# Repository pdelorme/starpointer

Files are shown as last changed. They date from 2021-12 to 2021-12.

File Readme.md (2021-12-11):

StarPointer
===========

StarPointer is a small 3D printed autonomous device that allows one to point and track sky objects (planets, shiny Messier objects, ISS) with a laser.

it's properies are :
- fully 3D printed.
- controlled by ESP8266 or ESP32
- motorized with 2 Stepper 28byj-48
- WIFI Access Point or Client
- Responsive Web interface.
- ISS tracking data auto-update.
- Dynamic tracking of objects.
- Persitence of configuration in EEPROM
- Low power (simple 5V powerpack)

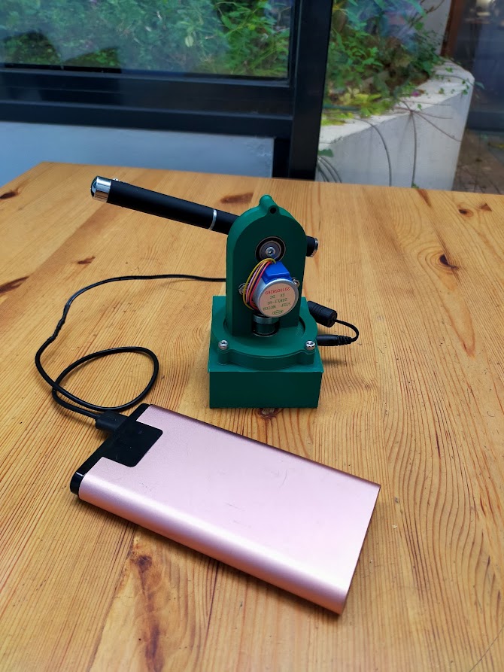
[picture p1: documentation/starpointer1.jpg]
Star pointer


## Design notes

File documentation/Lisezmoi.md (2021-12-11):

Documentation
===

StarPointer est concu pour etre calibré manuellement quelque soit son orientation.
Le seul prérequis est d'avoir l'etoile polaire en visuel.

Connexion
---
Lors de sa premiere mise sous tension le startPointer creera un Acces Point WIFI
- SSID : STAR_POINTER
- MdP  : 1234567890
- IP   : 192.168.4.1

Connectez vous-y avec votre navigateur PC ou mobile : http://192.168.4.1/

Configuration
---
StarTracker à besoin de connaitre votre position géographique et l'heure pour tous ses calculs astronomiques.

Dés votre connexion, le StarPointer recuperera l'heure de votre PC ou mobile pour se configurer.
Vous pouvez constater l'heure prise en compte sur l'interface.

Vous devrez configurer votre position géographique manuellement avec le dropdown de positions connues.

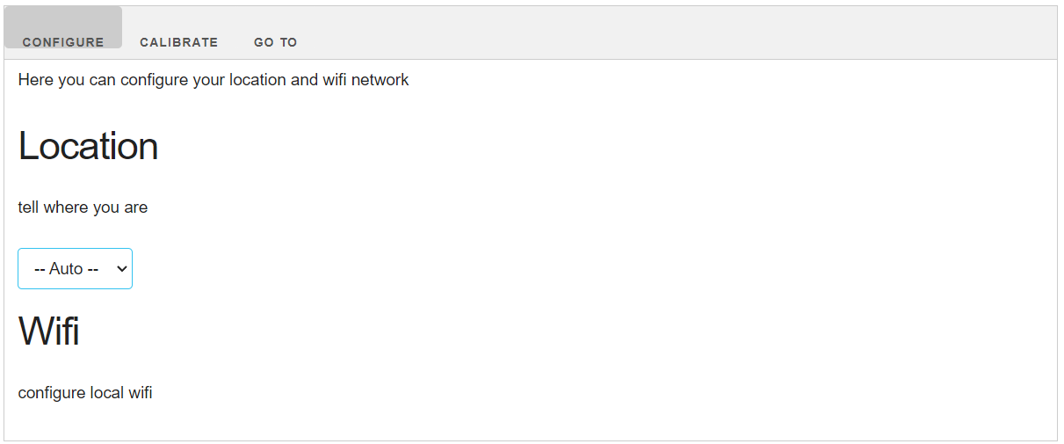
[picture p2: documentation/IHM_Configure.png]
Configure


Calibration
---
Une fois l'apareil configuré, vous devez le calibrer pour qu'il sache ou est le nord celeste.

Sur l'onglet calibration
  1. appuyez sur "Goto Polaris". Le startracker se déplacera vers ce qui est polaris pour lui. initialement cette position est aléatoire.
  2. orientez le startracker pour que le pointeur laser pointe aproximativement dans la direction du nord.
  3. à l'aide des touches UP, DOWN, LEFT, RIGH, déplacez le pointeur pour qu'il pointe le plus pécisément possible sur l'étoile polaire.
  4. une fois l'alignement satisfaisant, appuyez sur "set polaris position"
Le startracker est maintenant calibré.

Vous pouvez vérifier son bon fonctionnement grace aux boutons North, south, east, west, horizon et azimuth qui déplacerons le laser vers la dircetion choisie.

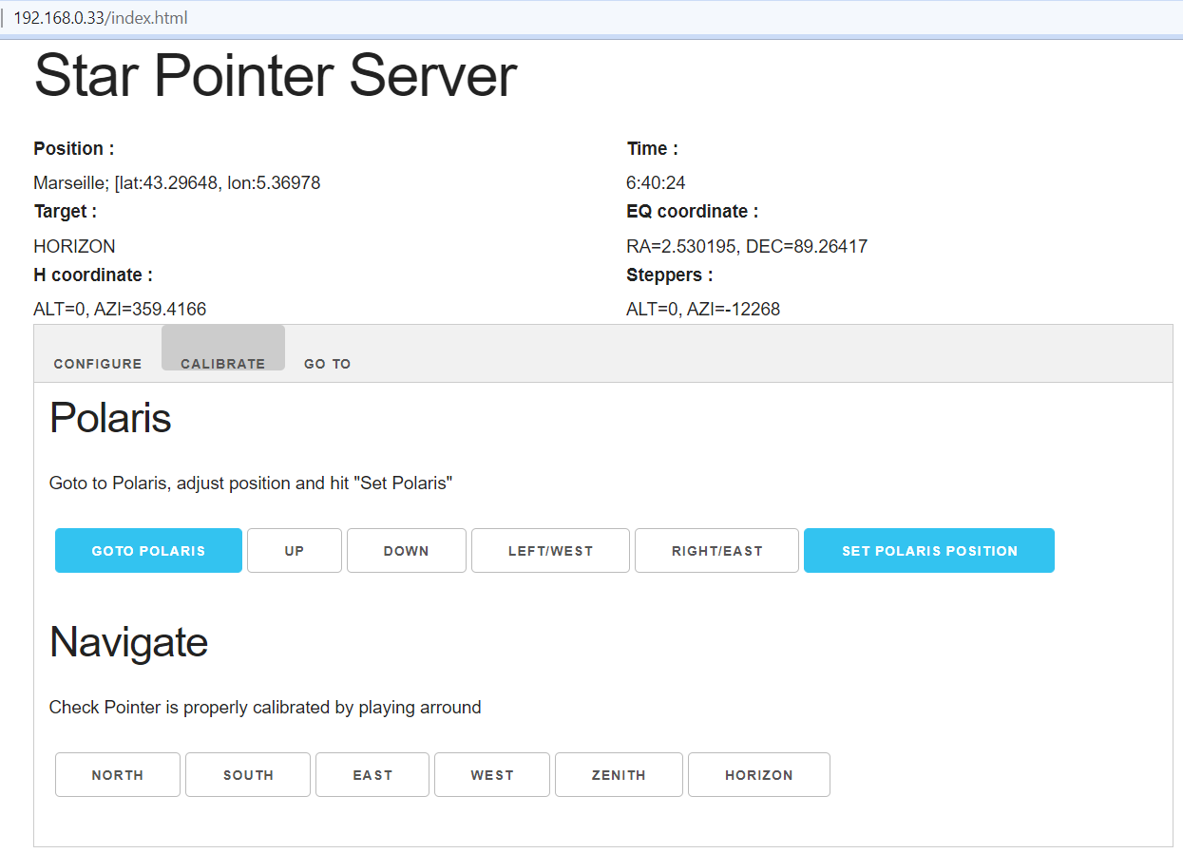
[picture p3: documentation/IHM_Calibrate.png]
Calibrate


Tracking
---
L'onglet goto sert à controler le startPointer une fois bien configuré.

Choisisez une target et laissez le starPointer aller à la cible puis la suivre.

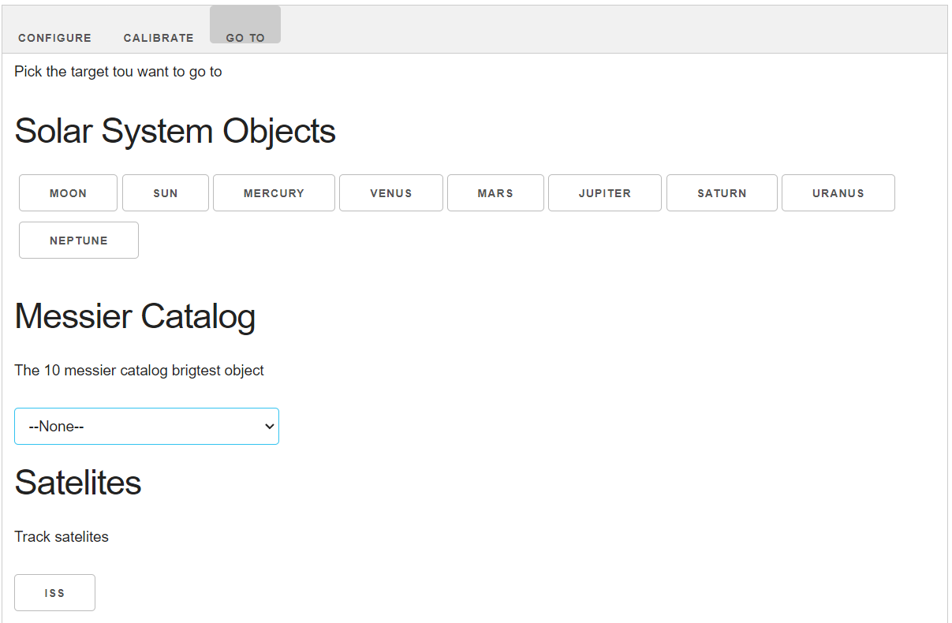
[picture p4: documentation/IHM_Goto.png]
Go To


Note
---
- Starpointer est contraint au dessus de l'horizon (une fois calibré). si votre cible est en dessous de l'horizon. il la suivra mais sans aller en dessous de l'horizon.

- Le calcul de la trajectoire de l'ISS dépend de données online qui doivent etre rafraichie régulierement pour etre valide. Pour se faire vous devrez connecter votre starpointer à internet avant une session d'observation.

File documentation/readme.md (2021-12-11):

Documentation
===

Starpointer is designed to be calibrated manually whatever his position and location is.
The only requierment is to be able to see polaris from the device.

Connexion
---
StarPointer will create the flowing WIFI access point at first boot or when the local AP cannot be fount.
- SSID : STAR_POINTER
- MdP  : 1234567890
- IP   : 192.168.4.1

Connect to StarPointer by going to http://192.168.4.1/ with your favorite browser on PC or mobile.

Configuration
---
StarPonter need to know where and when it is in order to do its astonomic calculations.

On connection, StarTracker will get time and location from your browser.
You can check that time is correct in the interface.
If geo-coordinate is not found, you can set it manually from the location drowpdown or by inputing your coordinates.

Configure

Calibration
---
Once configured, you must caibrate your device so it knows where celestial north is.

1. Go to "Calibration"
2. push "Goto Polaris". StarPointer will move to where it thinks polaris is (which is random at first)
3. move the device to point more or less north.
4. using the UP, DOWN, LEFT, RIGH buttons, move the poiter so it aligns perfectly with polaris.
5. push "set polaris position" when you are done.

StarPointer is now calibrated. 

You can use the North, south, east, west, horizon and azimuth buttons to check the StarPointer is behaving as exppected.

Calibrate

Tracking
---
This tab is for pointing the device at some space objects.

Pick the object you want to point to and StarPointer will move to it.
Once aligned with the target StarPointer will stay in synch and will update it pointing every seconds.

Go To

Note
---
- Starpointer is constrained above horizon (once calibrated). If your target is below the horizon, it will track it while staying stuck at the horizon level.
- ISS trajectory needs some fresh online update to be accurate. Therefore StarPointer has to be connected to local Wifi network in order to refresh its reference data. It'll try to do so each time you connect to a local network.

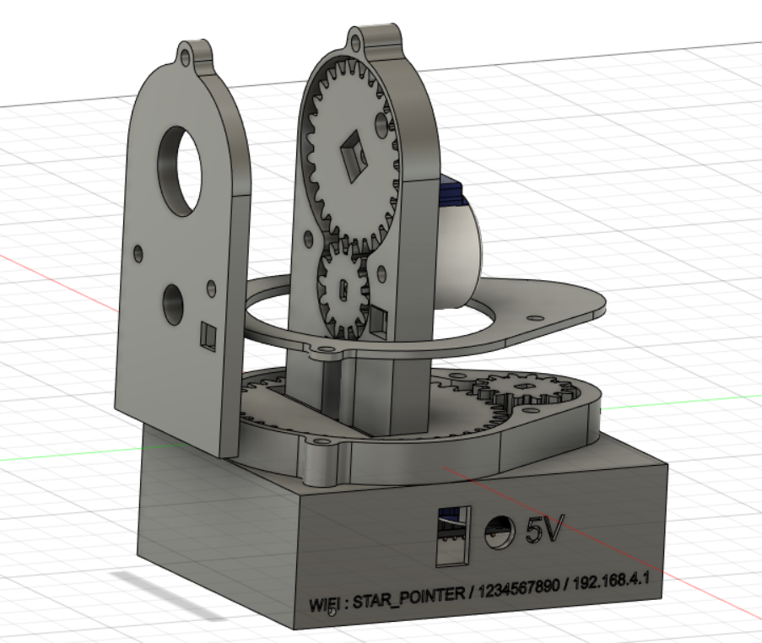
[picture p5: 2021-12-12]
3d/3DModel.png

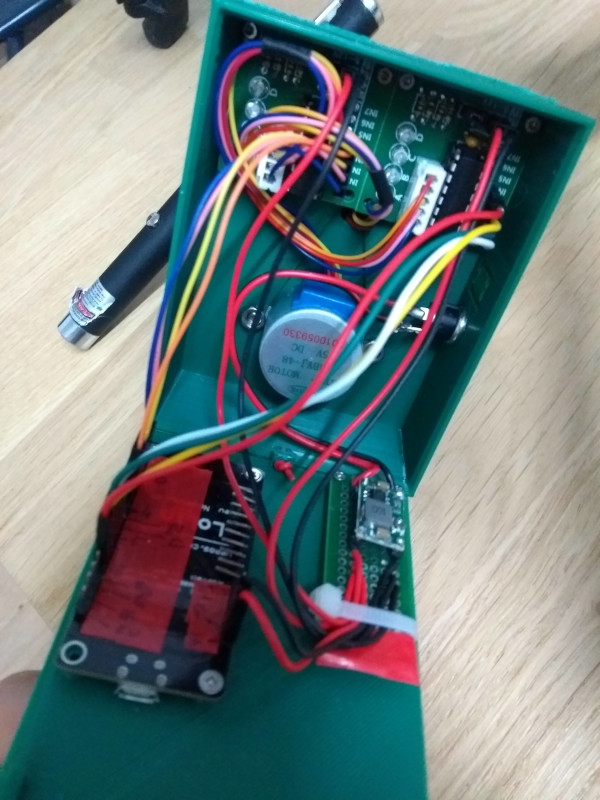
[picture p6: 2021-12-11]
fritzing/Photo inside.jpg

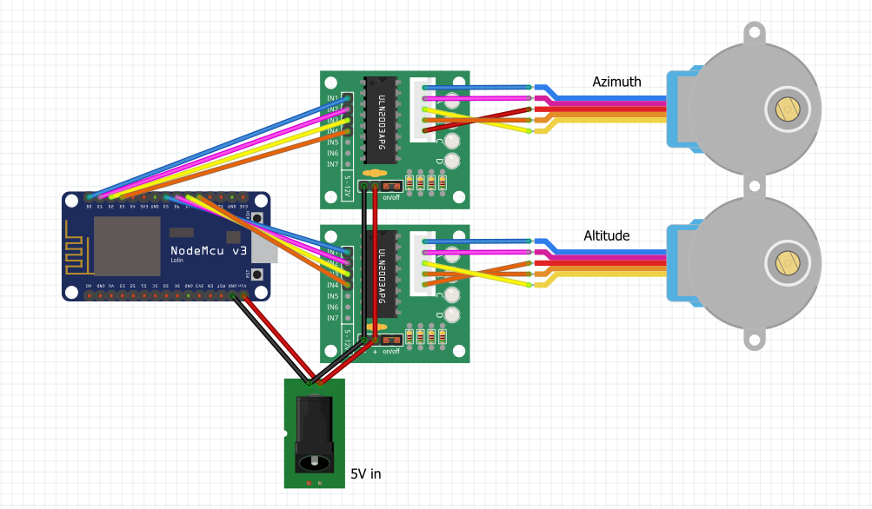
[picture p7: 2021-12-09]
documentation/Schema v1.png

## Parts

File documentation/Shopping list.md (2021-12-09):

Shopping list
===

Stylo Laser Vert de Haute Puissance de 5MW et 650 nm
https://fr.aliexpress.com/item/1005002921019708.html

Module Laser vert 532nm 35mW 2.2V, en cuivre
https://fr.aliexpress.com/item/1005002430590788.html

2 moteur pas à pas à engrenage 28 byj-48, 5V + carte de controle ULN2003
https://fr.aliexpress.com/item/33036332558.html

Lolin NodeMcu V3, ESP8266
https://fr.aliexpress.com/item/33053690164.html

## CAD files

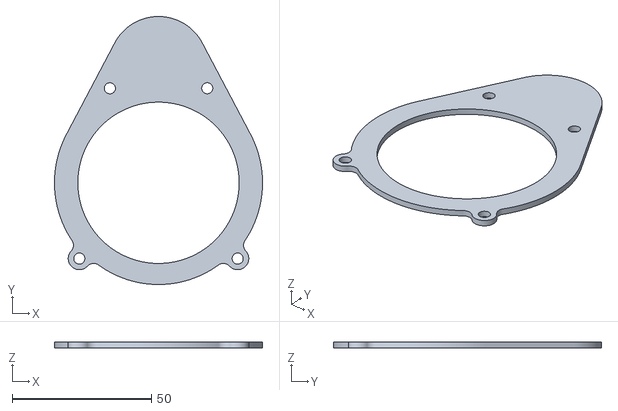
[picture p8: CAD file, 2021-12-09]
3d/stl/Main Body Cover.stl
74.8 x 96.4 x 2.00

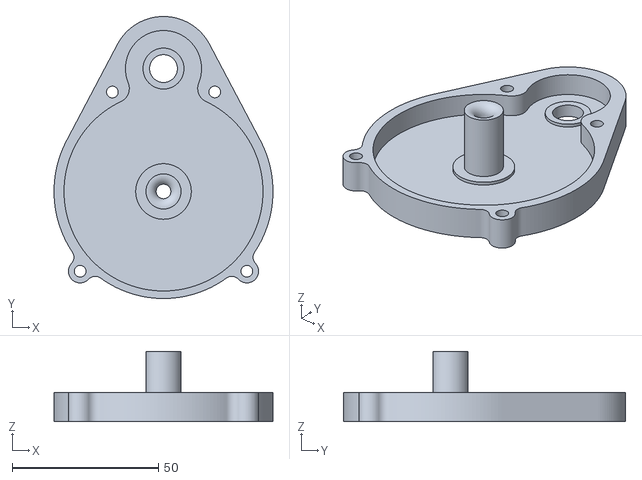
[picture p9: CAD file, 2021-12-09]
3d/stl/Main Body.stl
74.8 x 96.4 x 24.0

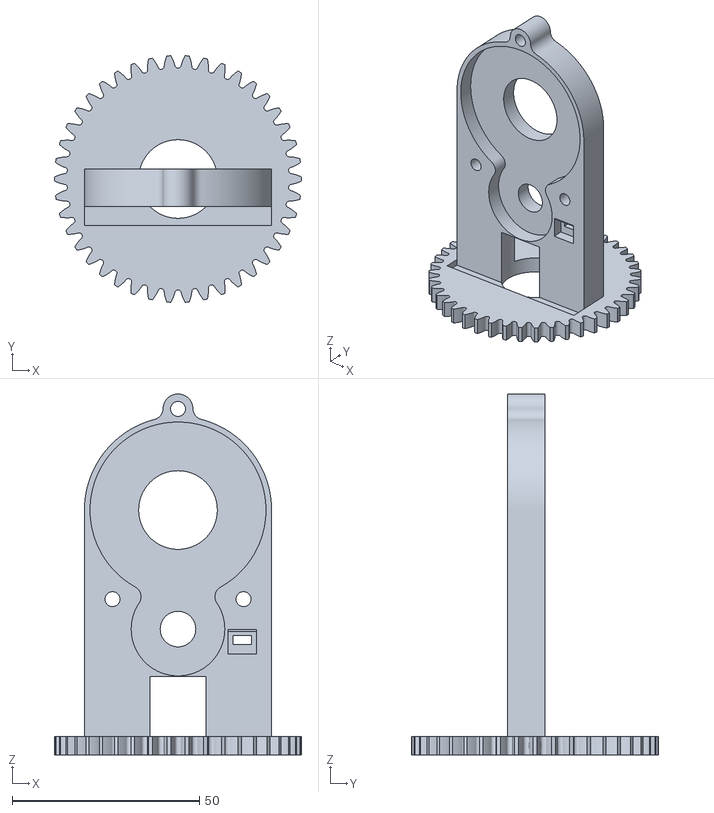
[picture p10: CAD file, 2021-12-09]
3d/stl/Big H Gear (42 teeth).stl
66.0 x 65.9 x 96.4

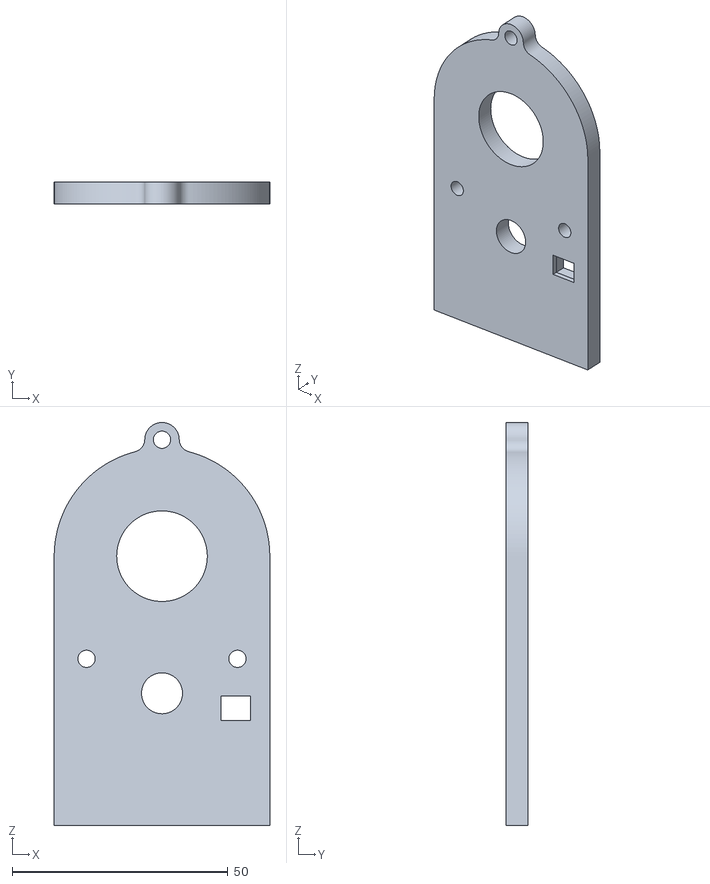
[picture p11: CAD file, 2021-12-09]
3d/stl/Top seal.stl
50.0 x 5.00 x 93.4

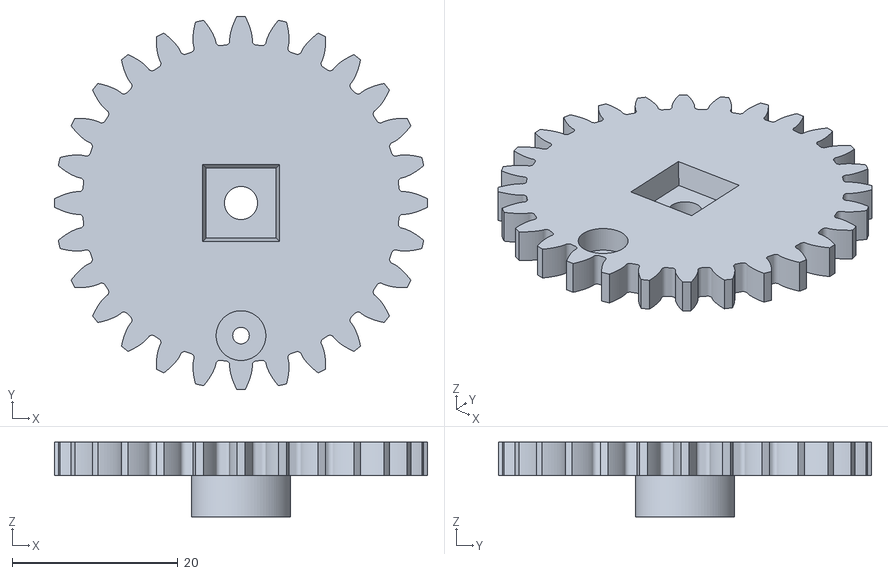
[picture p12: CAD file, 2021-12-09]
3d/stl/Spur Gear (28 teeth).stl
45.0 x 45.0 x 9.00

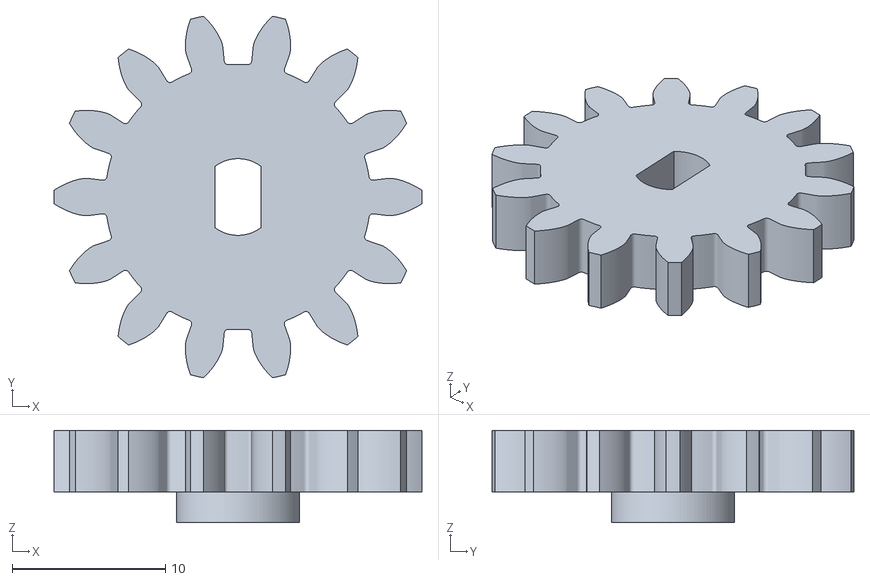
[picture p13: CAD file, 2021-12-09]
3d/stl/Small H Gear (14 teeth).stl
24.0 x 23.6 x 6.00

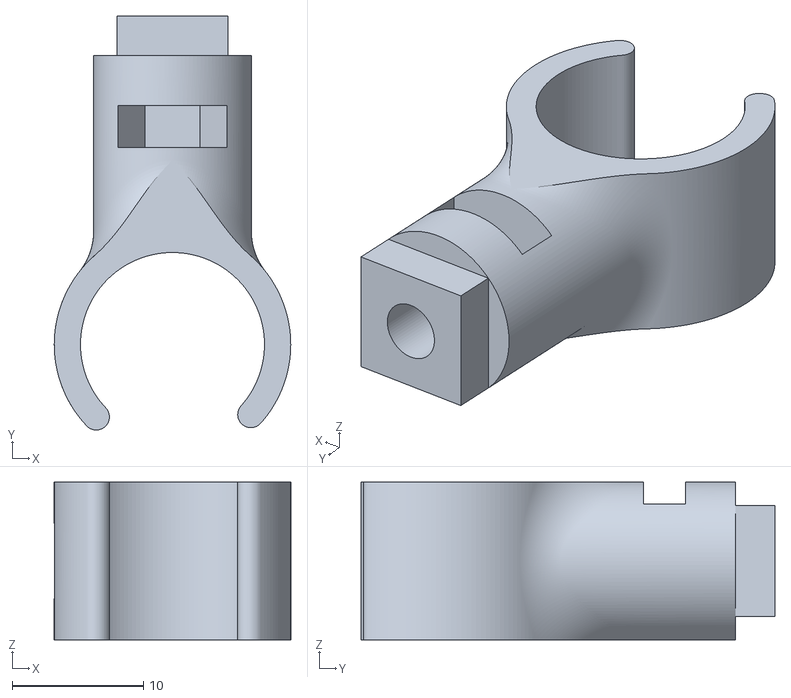
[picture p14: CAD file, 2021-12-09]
3d/stl/Pointer.stl
18.0 x 31.5 x 12.0

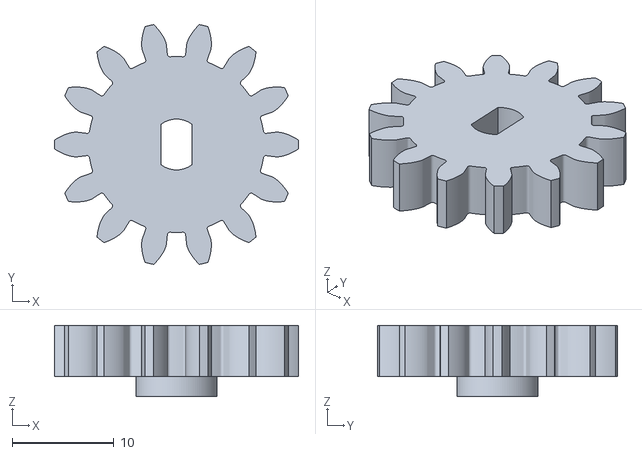
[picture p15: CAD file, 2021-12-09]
3d/stl/Small H Gear (14 teeth) 5mm.stl
24.0 x 23.6 x 7.00

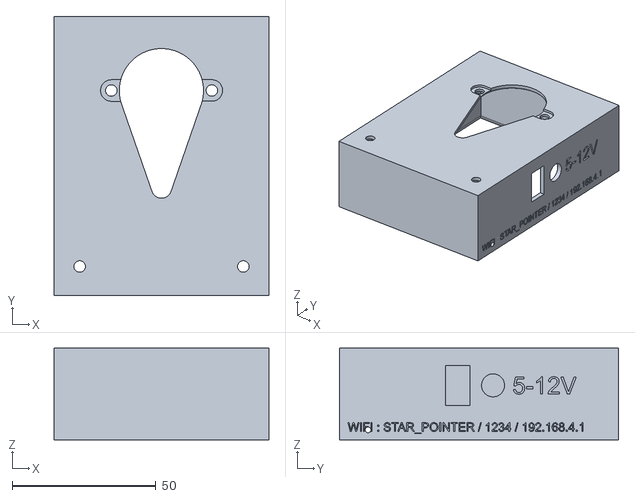
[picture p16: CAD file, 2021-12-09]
3d/stl/box.stl
74.8 x 97.2 x 32.0

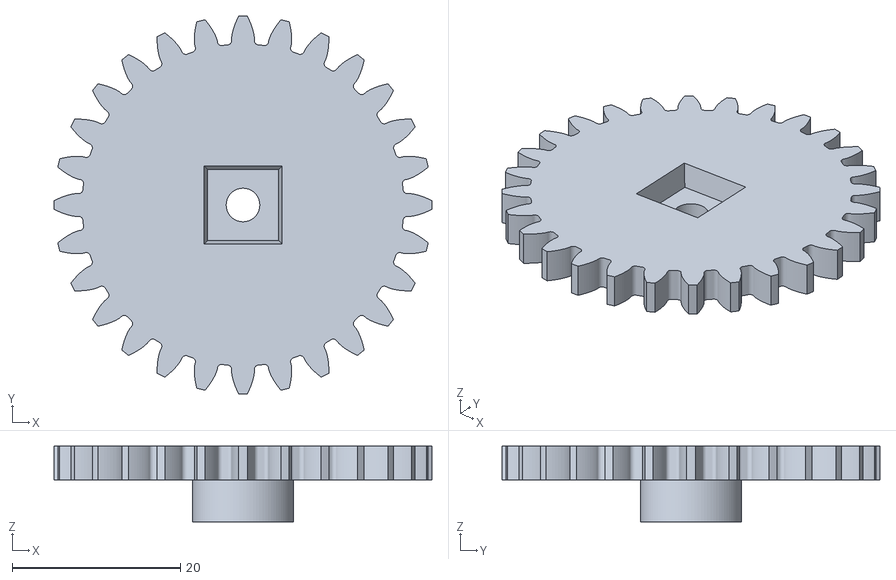
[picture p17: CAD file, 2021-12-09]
3d/stl/Big V Gear (28 teeth).stl
45.0 x 45.0 x 9.00

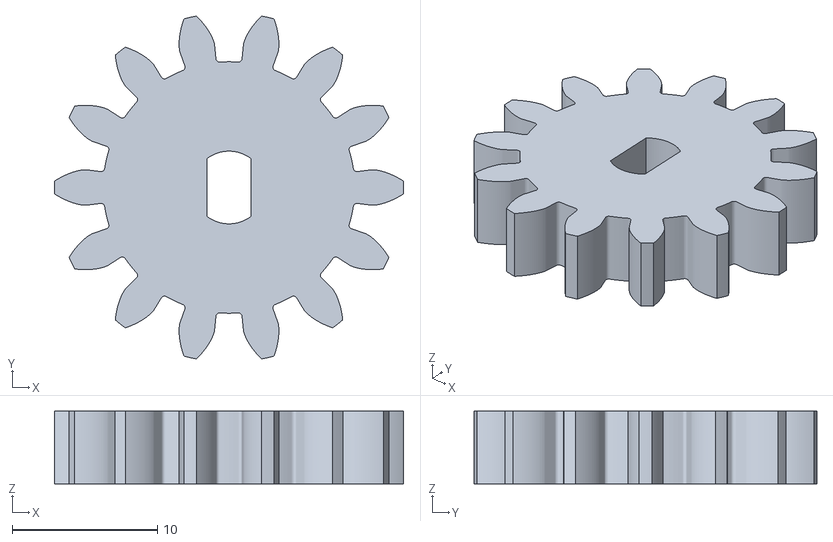
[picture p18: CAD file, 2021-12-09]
3d/stl/Small v Gear (14 teeth).stl
24.0 x 23.6 x 5.00

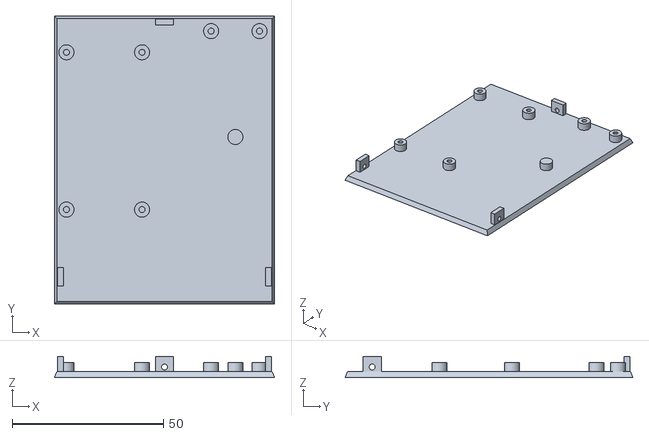
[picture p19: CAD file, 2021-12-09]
3d/stl/box lid.stl
72.8 x 95.2 x 7.00

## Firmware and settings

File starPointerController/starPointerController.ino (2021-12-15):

/*********
  Patrice Delorme
  Controle le star pointer depuis le WIFI.
*********/
#define TEST 0 // set to 1 for unit testing.
#define DEBUG 1 // set to 1 for debug logging.

// Import required libraries
#include <ESP8266WiFi.h>
#include <ESPAsyncTCP.h>
#include <ESPAsyncWebServer.h>
#include <ESP8266HTTPClient.h>
#include <ArduinoJson.h>
#include <Ephemeris.h>
#include <TimeLib.h>
#include <AccelStepper.h>
#include "FS.h"
#include <Sgp4.h>
#include <EEPROM.h>
#if TEST == 1
#include <ArduinoUnit.h>
#endif

AccelStepper aziStepper(AccelStepper::HALF4WIRE, D1, D3, D2, D4);
AccelStepper altStepper(AccelStepper::HALF4WIRE, D5, D7, D6, D8);
#define LASER_PIN D0

enum TargetType {
  NoTarget = 0,
  ISSTarget = 1,
  SolarSystemTarget = 2,
  StellarTarget = 3
};

TargetType targetType = NoTarget;

// if -1 this is not a solar object.
SolarSystemObjectIndex solarSystemObjectIndex = Earth;
EquatorialCoordinates targetEqCoord;
HorizontalCoordinates targetHCoord;
String targetName = "Aucune";
unsigned long updateMillis = 0;

#if TEST == 0
void setup(){
  // Serial port for debugging purposes
  Serial.begin(115200);
  setupEEPROM();
  setupWifi();
  //setupSatTrack();
  setupWebserver();
  setupStarpointer();
}

void loop() {
  loopWebserver();
  loopStarpointer();
  // loopSatTrack();
}
#else
void setup(){
  Serial.begin(115200);
  setupEEPROM();
}

void loop(){
  Test::run();
}
#endif

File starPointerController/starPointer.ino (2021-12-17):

const int RoundSteps = 2048;
const int azi360Steps = -RoundSteps * 6;
const int alt360Steps = RoundSteps * 4;

// laser is pointing to polaris.
// set pointer steps to hypothetical 0.
void setLaserPositionFromPolaris(){
  HorizontalCoordinates polarisHCoord = Ephemeris::equatorialToHorizontalCoordinatesAtDateAndTime(polarisEqCoord, day(), month(), year(), hour(), minute(), second());
  aziStepper.setCurrentPosition(polarisHCoord.azi/360*azi360Steps); // steps from azimuth.
  altStepper.setCurrentPosition(polarisHCoord.alt/360*alt360Steps); // Steps from altitude.
}

void goToEqCoords(EquatorialCoordinates eqCoordinates){
  targetEqCoord = eqCoordinates;
  HorizontalCoordinates targetHCoord = Ephemeris::equatorialToHorizontalCoordinatesAtDateAndTime(eqCoordinates, day(), month(), year(), hour(), minute(), second());
  goToHCoords(targetHCoord.alt,targetHCoord.azi); // Steps from altitude.
}

void goToHCoords(float alt, float azi){
  // min altitude is 0.
  if(alt<0) alt = 0;
  if(alt>180) alt = 180;
  altStepper.moveTo(alt/360*alt360Steps); // Steps from altitude.  
  aziStepper.moveTo(azi/360*azi360Steps); // steps from azimuth.
  targetHCoord = {alt, azi};
}

// goto 0,0
void goHome(){
  goToHCoords(0,0);
}

void laserOn(boolean isOn){
  digitalWrite (LASER_PIN, isOn?HIGH:LOW);
}

void up(int steps)   {altStepper.moveTo(altStepper.targetPosition()+steps);}
void down(int steps) {altStepper.moveTo(altStepper.targetPosition()-steps);}
void left(int steps) {aziStepper.moveTo(aziStepper.targetPosition()+steps);}
void right(int steps){aziStepper.moveTo(aziStepper.targetPosition()-steps);}

void setupStarpointer(){
  // steppers
  altStepper.setMaxSpeed(400);
  altStepper.setAcceleration(50);
  aziStepper.setMaxSpeed(400);
  aziStepper.setAcceleration(50);
  // laser
  pinMode(LASER_PIN, OUTPUT);
  // location
  String location = readStringFromEEPROM(EEPROM_LOC_OFFSET);
  if(location=="MANUAL"){
    float lat = readFloatFromEEPROM(EEPROM_LAT_OFFSET);
    float lon = readFloatFromEEPROM(EEPROM_LON_OFFSET);
    setPositionOnEarth(lat, lon, false);
  } else {
    setLocationOnEarth(getLocation(location), false); 
  }
}

void setPositionOnEarth(float lat, float lon, boolean save){
  Location location = {"MANUAL", "Manuel", {lon, lat}};
  setLocationOnEarth(location, save);
}

Location getLocationOnEarth(){
  String locCode = readStringFromEEPROM(EEPROM_LOC_OFFSET);
  if(locCode=="MANUAL"){
    float lat = readFloatFromEEPROM(EEPROM_LAT_OFFSET);
    float lon = readFloatFromEEPROM(EEPROM_LON_OFFSET);
    Location location = {"MANUAL", "Manuel", {lon, lat}};
    return location;
  } else {
    return getLocation(locCode);
  }
}
void setLocationOnEarth(Location location, boolean save){
  debugln("setLocationOnEarth:"+location.name);
  locationOnEarth = location;
  if(save){
    writeStringToEEPROM(EEPROM_LOC_OFFSET, location.code);
    writeFloatToEEPROM(EEPROM_LAT_OFFSET, location.geoCoords.lat);
    writeFloatToEEPROM(EEPROM_LON_OFFSET, location.geoCoords.lon);
  }
  Ephemeris::setLocationOnEarth(location.geoCoords.lat, location.geoCoords.lon);
}

unsigned long solarSystemUpdateMillis = 0;
void loopStarpointer(){
  if(targetType == SolarSystemTarget && (millis()-solarSystemUpdateMillis>1000)){
    solarSystemUpdateMillis = millis();
    SolarSystemObject solarSystemObject = Ephemeris::solarSystemObjectAtDateAndTime(solarSystemObjectIndex, day(), month(), year(), hour(), minute(), second());
    goToEqCoords(solarSystemObject.equaCoordinates);
  }
  altStepper.run();
  aziStepper.run();
}

/**
 * Unit Testing.
 */
#if TEST == 1

test(setLocationOnEarthFalse){
  Location loc = getLocation("LYON");
  setLocationOnEarth(loc, false);
  assertEqual(loc.name, locationOnEarth.name);
  assertEqual(loc.code, locationOnEarth.code);
  assertEqual(loc.geoCoords.lat, locationOnEarth.geoCoords.lat);
  assertEqual(loc.geoCoords.lon, locationOnEarth.geoCoords.lon);
}

test(setLocationOnEarthTrue){
  Location loc = getLocation("BREST");
  setLocationOnEarth(loc, true);
  Location loc2 = getLocationOnEarth();
  assertEqual(loc.name, loc2.name);
  assertEqual(loc.code, loc2.code);
  assertEqual(loc.geoCoords.lat, loc2.geoCoords.lat);
  assertEqual(loc.geoCoords.lon, loc2.geoCoords.lon);
}
#endif

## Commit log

2021-12-09 stl files
    [Big H Gear (42 teeth).stl, Big V Gear (28 teeth).stl, Main Body Cover.stl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]
2021-12-09 stl v2
    [Big H Gear (42 teeth).stl, Top seal.stl]
2021-12-09 ajout de readme
2021-12-09 fritzing schemas
    [Star Pointer v1.fzz]
2021-12-09 ajout de documentation
2021-12-09 Ajout de shopping list
2021-12-09 ajout photo circuit
2021-12-12 fixing eepromUtils + added unit testing
    [eepromUtils.ino, starPointerController.ino]
2021-12-15 steppers on D1-D4,D5-D8 + LASER_PIN=D0
2021-12-17 fixed GeoData + Unit Test
    [data.ino]
2021-12-17 Added laser switch, reworked command parsing, fixed HTML
    [starPointer.ino, webServer.ino]
